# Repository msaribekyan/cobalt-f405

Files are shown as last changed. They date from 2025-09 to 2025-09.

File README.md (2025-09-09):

# Cobalt F405

## An open source flight controller based on the STM32F405 microcontroller

Custom designed flight controller for quadcopters and more.

<div style="text-align:center;">
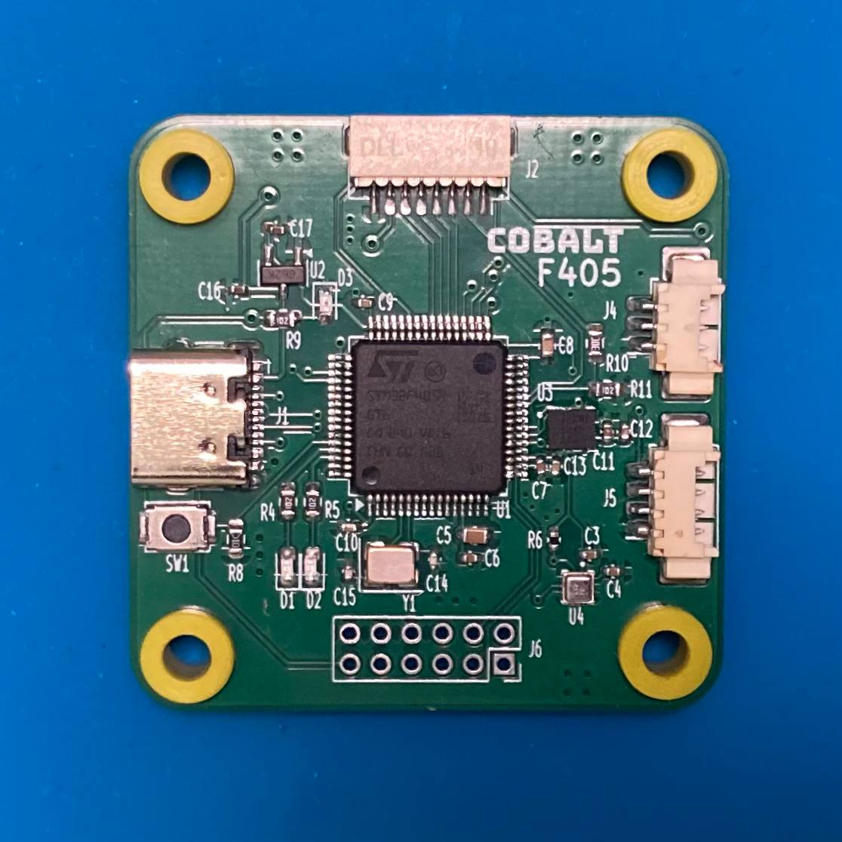
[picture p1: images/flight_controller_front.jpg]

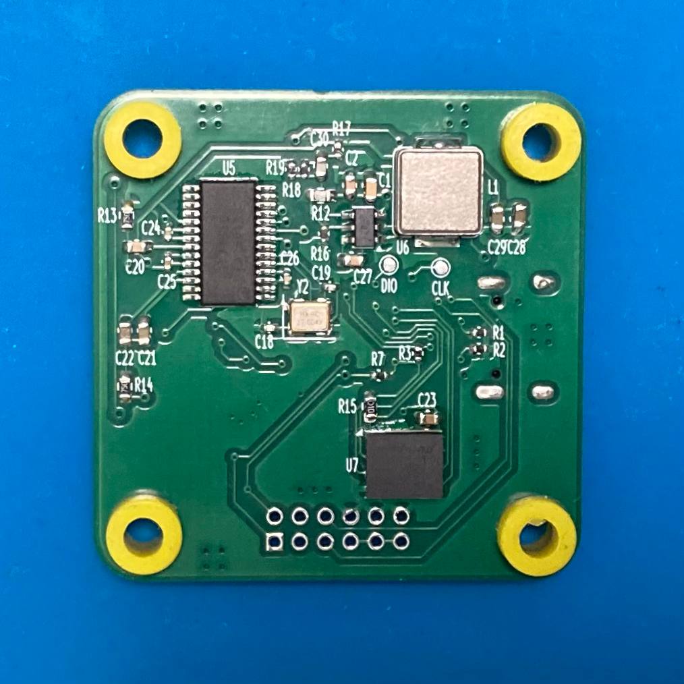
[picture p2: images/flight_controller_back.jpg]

</div>

## Features

Cobalt F405 flight controller has the following features:
- 4 motor outputs
- barometer and blackbox
- analog on-screen display
- easy-to-use connectors for camera and VTx
- USB Type-C connector for configuration
- high power 5 volt regulator

## Firmware

The flight controller was tested with the [Betaflight](https://github.com/betaflight/betaflight) firmware.

<div style="text-align:center;">
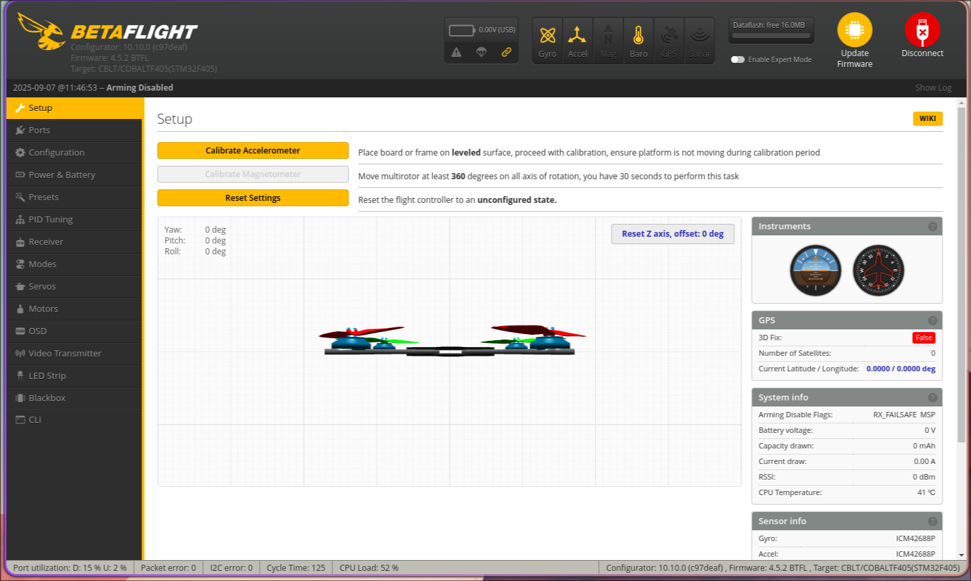
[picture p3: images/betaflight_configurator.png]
Betaflight configurator

</div>

## Designing

KiCad was used for designing the schematic and the PCB.

### Schematic

<div style="text-align:center;">
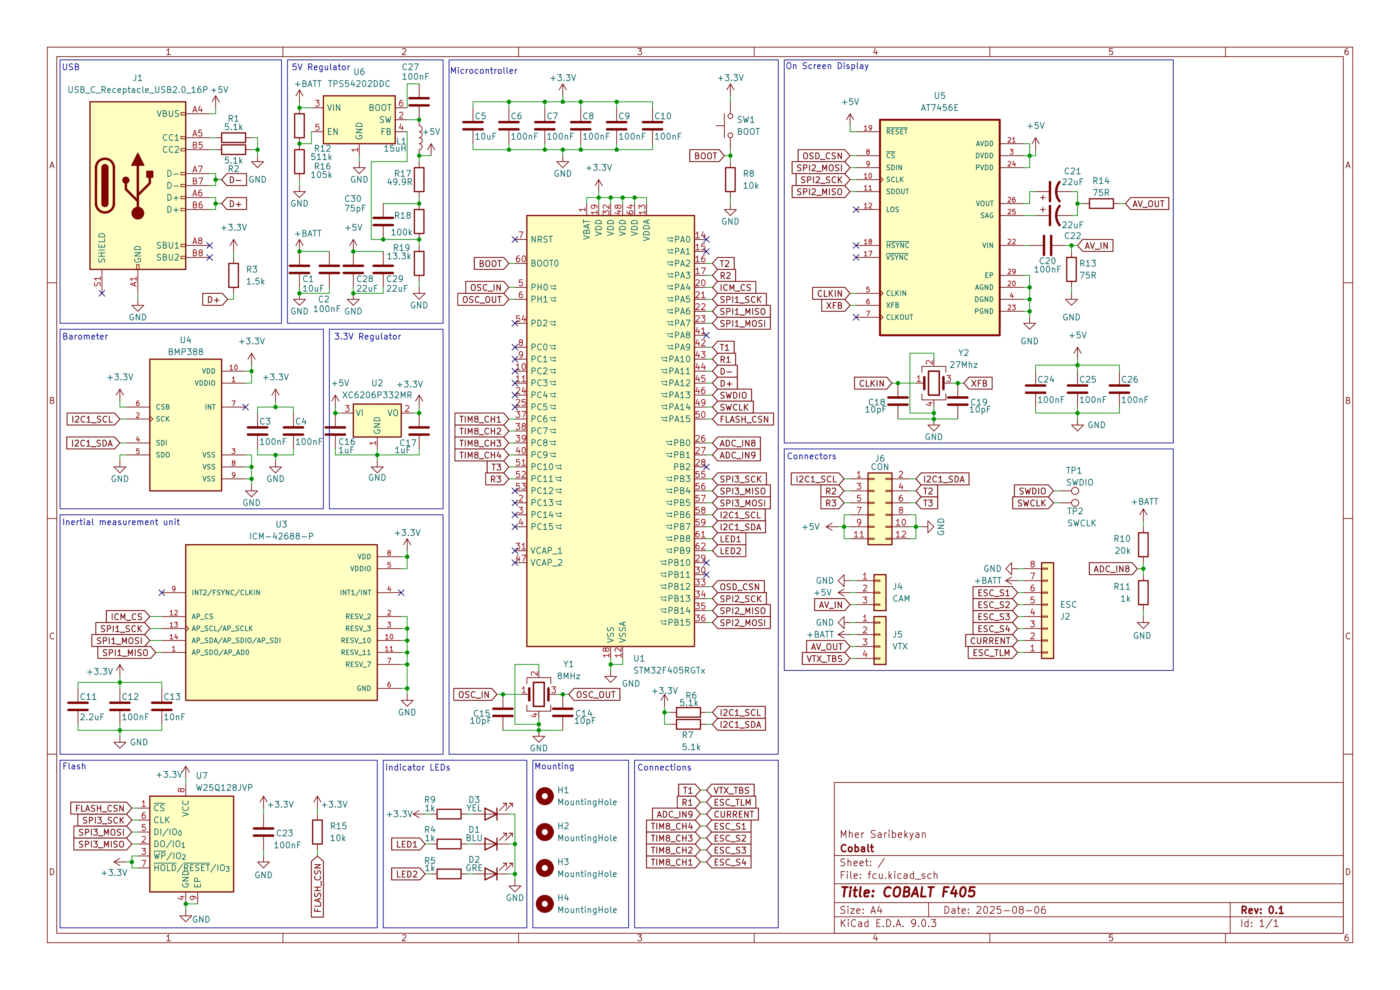
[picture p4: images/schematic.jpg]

</div>

### PCB 3D model

<div style="text-align:center;">
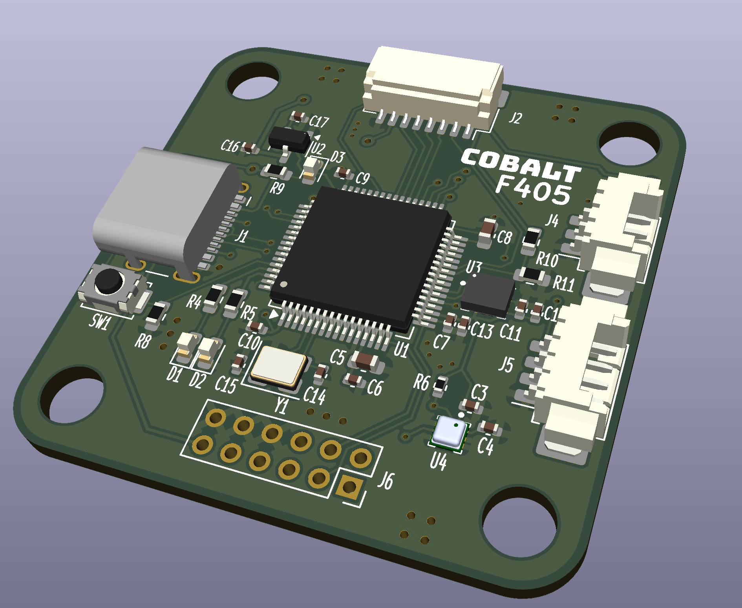
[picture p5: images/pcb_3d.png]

</div>

## Further improvements

### Microcontroller

Although the STM32F405 is still a good choice for flight controllers today, other more powerful microcontrollers also exist. [Betaflight guidlines](https://betaflight.com/docs/development/manufacturer/manufacturer-design-guidelines) suggest not using more than 4 motor outputs for STM32F4 or STM32F7 type microcontrollers.

### PCB

Two layer PCB is fine, however going to a four layer PCB with ground planes inside would reduce electrical noise, which would benefit the microcontroller and the on-board sensors.

### 9 volt regulator

Some external peripherals require higher voltage than 5 volts, however cannot accept 25 volts straight from a 6S battery. A 9 volt regulator can be added to solve this issue.

### More pads and connectors

More pads on the PCB would make it more flexible and easier to use in application. Camera and VTx connectors can be moved to more suitable locations and a connector for the radio receiver could be added.

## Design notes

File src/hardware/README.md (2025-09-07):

# The hardware

The PCB was design using [KiCad](https://gitlab.com/kicad/code/kicad), an open source schematic and PCB design software.

## Microcontroller: STM32F405RGT6

Betaflight has a list of supported microcontrollers and the STM32F405RGT6, because it is the most common and economical choice while providing enough performance.

## Inertial measurement unit: ICM-42688-P

The [Betaflight Flight Controller Manufacturer Design Guidelines](https://betaflight.com/docs/development/manufacturer/manufacturer-design-guidelines) strongly recommends against using the MPU6000 as it is end-of-life. Instead ICM-42688-P is suggested.

## Barometer: BMP388

Newer model of the BMP180 and BMP280 barometers.

## Blackbox: W25Q128JVP

Winbond W25Q128JVPIQ is a cheap and common 16 MB NOR Flash chip, with a small WSON-8 footprint.

## On-screen display: AT7456E

The flight controller has an on-screen display, for use with analog video. AT7456E is the standard choice.

## Connectors

An 8 pin JST connector is the standard for connecting to the ESC. Telemetry data is connected to UART 1 RX. The two Molex PicoBlade connectors are for the camera and the video transmitter (VTx). The camera connector passes 5 volt power, while the VTx connector passes battery power for more powerful VTx and also has a SmartAudio pin connected to UART 1 TX.

## UART, I2C and power outputs

UARTs 2 and 3 are available on the solder points, along with the I2C bus and three pairs of 5 volt and ground connections.

## PCB

## Front layers

<div style="text-align:center;">
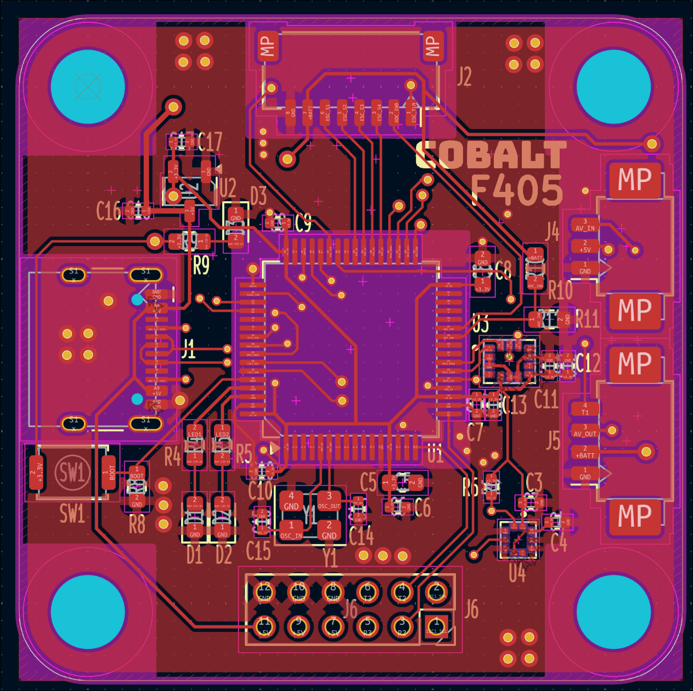
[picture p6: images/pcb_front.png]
PCB front layers

</div>

### Back layers

<div style="text-align:center;">
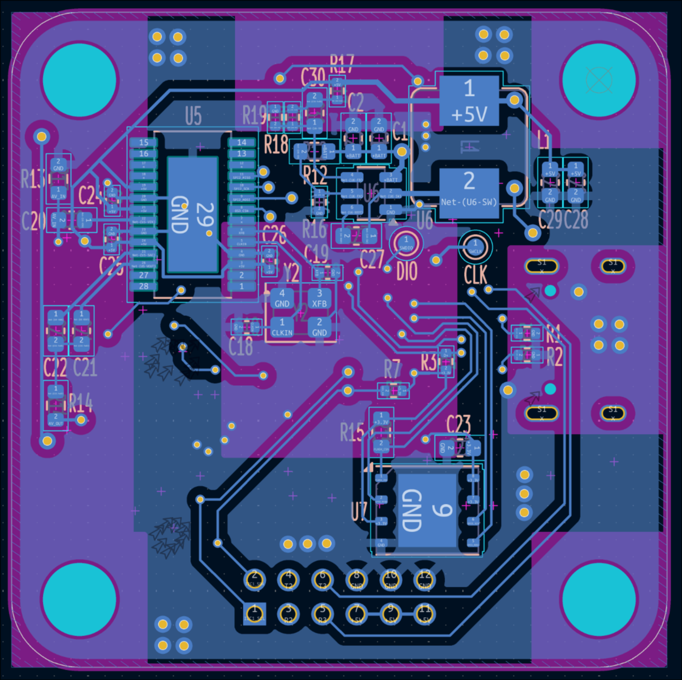
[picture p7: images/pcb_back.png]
PCB back layers

</div>

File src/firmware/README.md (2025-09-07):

# The firmware

The [Betaflight](https://github.com/betaflight/betaflight) firmware was used and tested for the flight controller. The compiled .hex file can be used to flash the firmware, however the configuration files are also avaible, in case you want to compile yourself.

## How to flash

The easiest way of flashing is using the STM32CubeProgrammer, however other methods also exist e.g. using [stlink utility](https://github.com/stlink-org/stlink) or [OpenOCD](https://github.com/openocd-org/openocd).

### Step 1
Install [STM32CubeProgrammer](https://www.st.com/en/development-tools/stm32cubeprog.html). 

### Step 2
While holding the button on the flight controller plug the USB-C cable, connect to the computer and release the button. This puts the microcontroller in DFU mode and allows flashing over USB.

### Step 3

Open STM32CubeProgrammer and from the dropdown select USB, then a device should appear in the Port section. If not, redo the Step 2, until it appears.

<div style="text-align:center;">
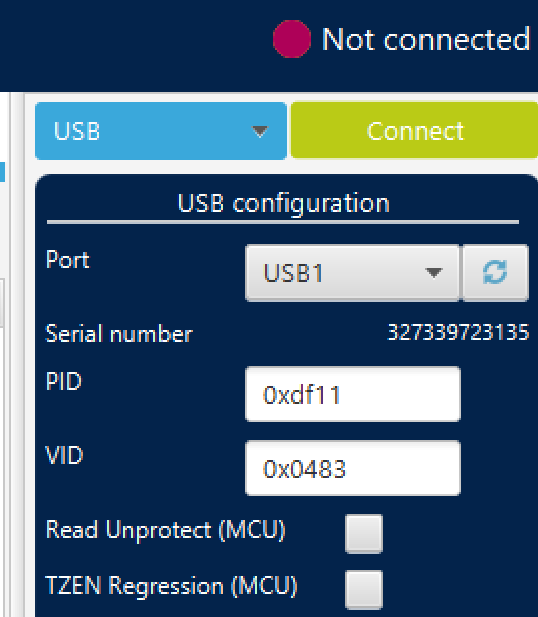
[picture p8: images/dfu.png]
Programmer DFU

</div>

Click connect.

### Step 3

Go the the Erasing & Programming tab. Click on Full chip erase.

<div style="text-align:center;">
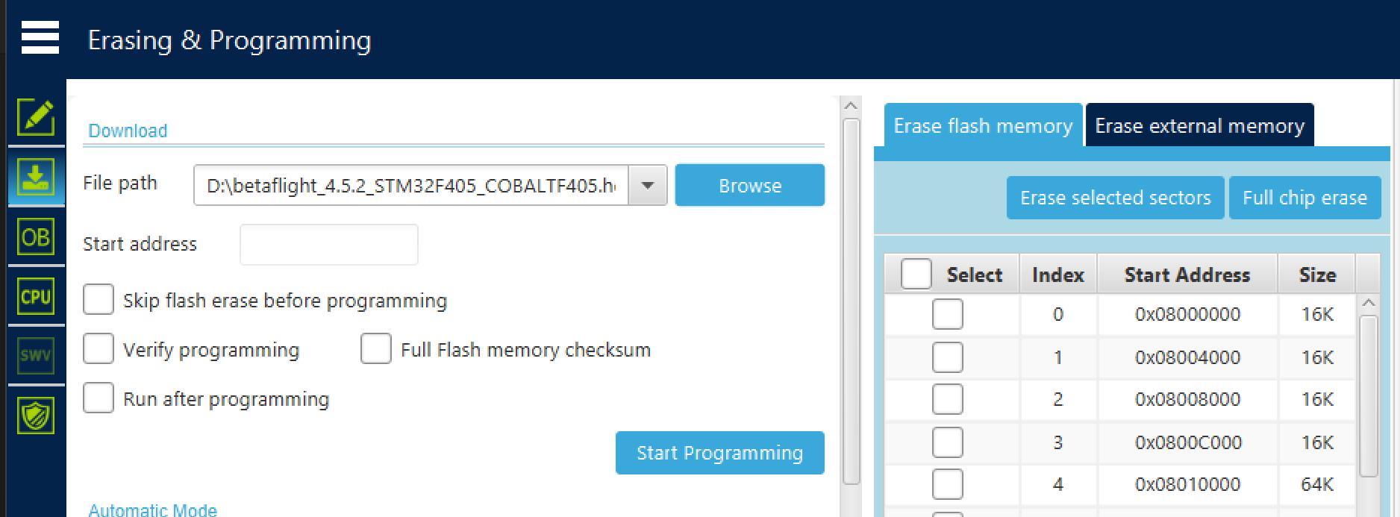
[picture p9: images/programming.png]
Programming tab

</div>

After the chip erase, select the .hex file included in the repository and click Start Programming. Wait until the firware is completely flashed, it may take a while.

### Done

Unplug and replug the USB cable. Now you should be able to connect to it using the [Betaflight App](https://github.com/betaflight/betaflight-configurator).

<div style="text-align:center;">
Betaflight configurator
</div>

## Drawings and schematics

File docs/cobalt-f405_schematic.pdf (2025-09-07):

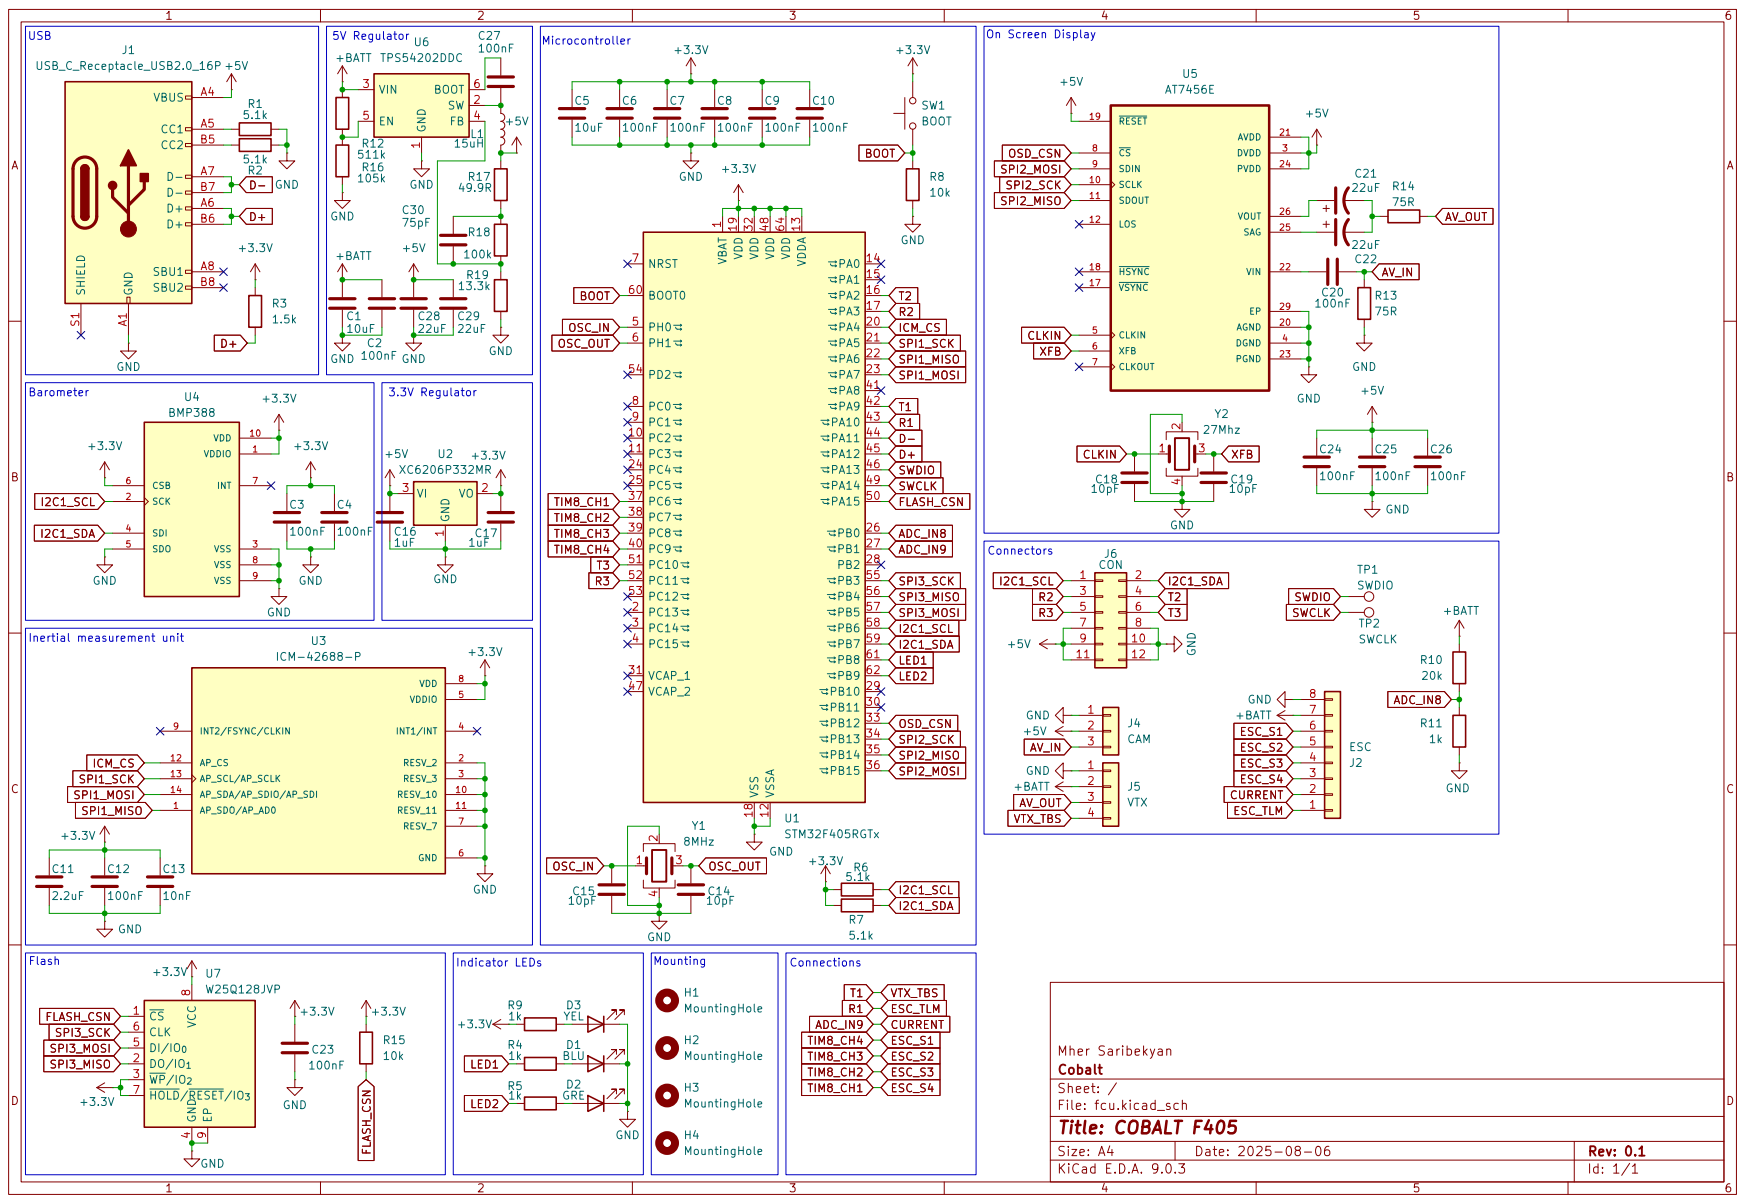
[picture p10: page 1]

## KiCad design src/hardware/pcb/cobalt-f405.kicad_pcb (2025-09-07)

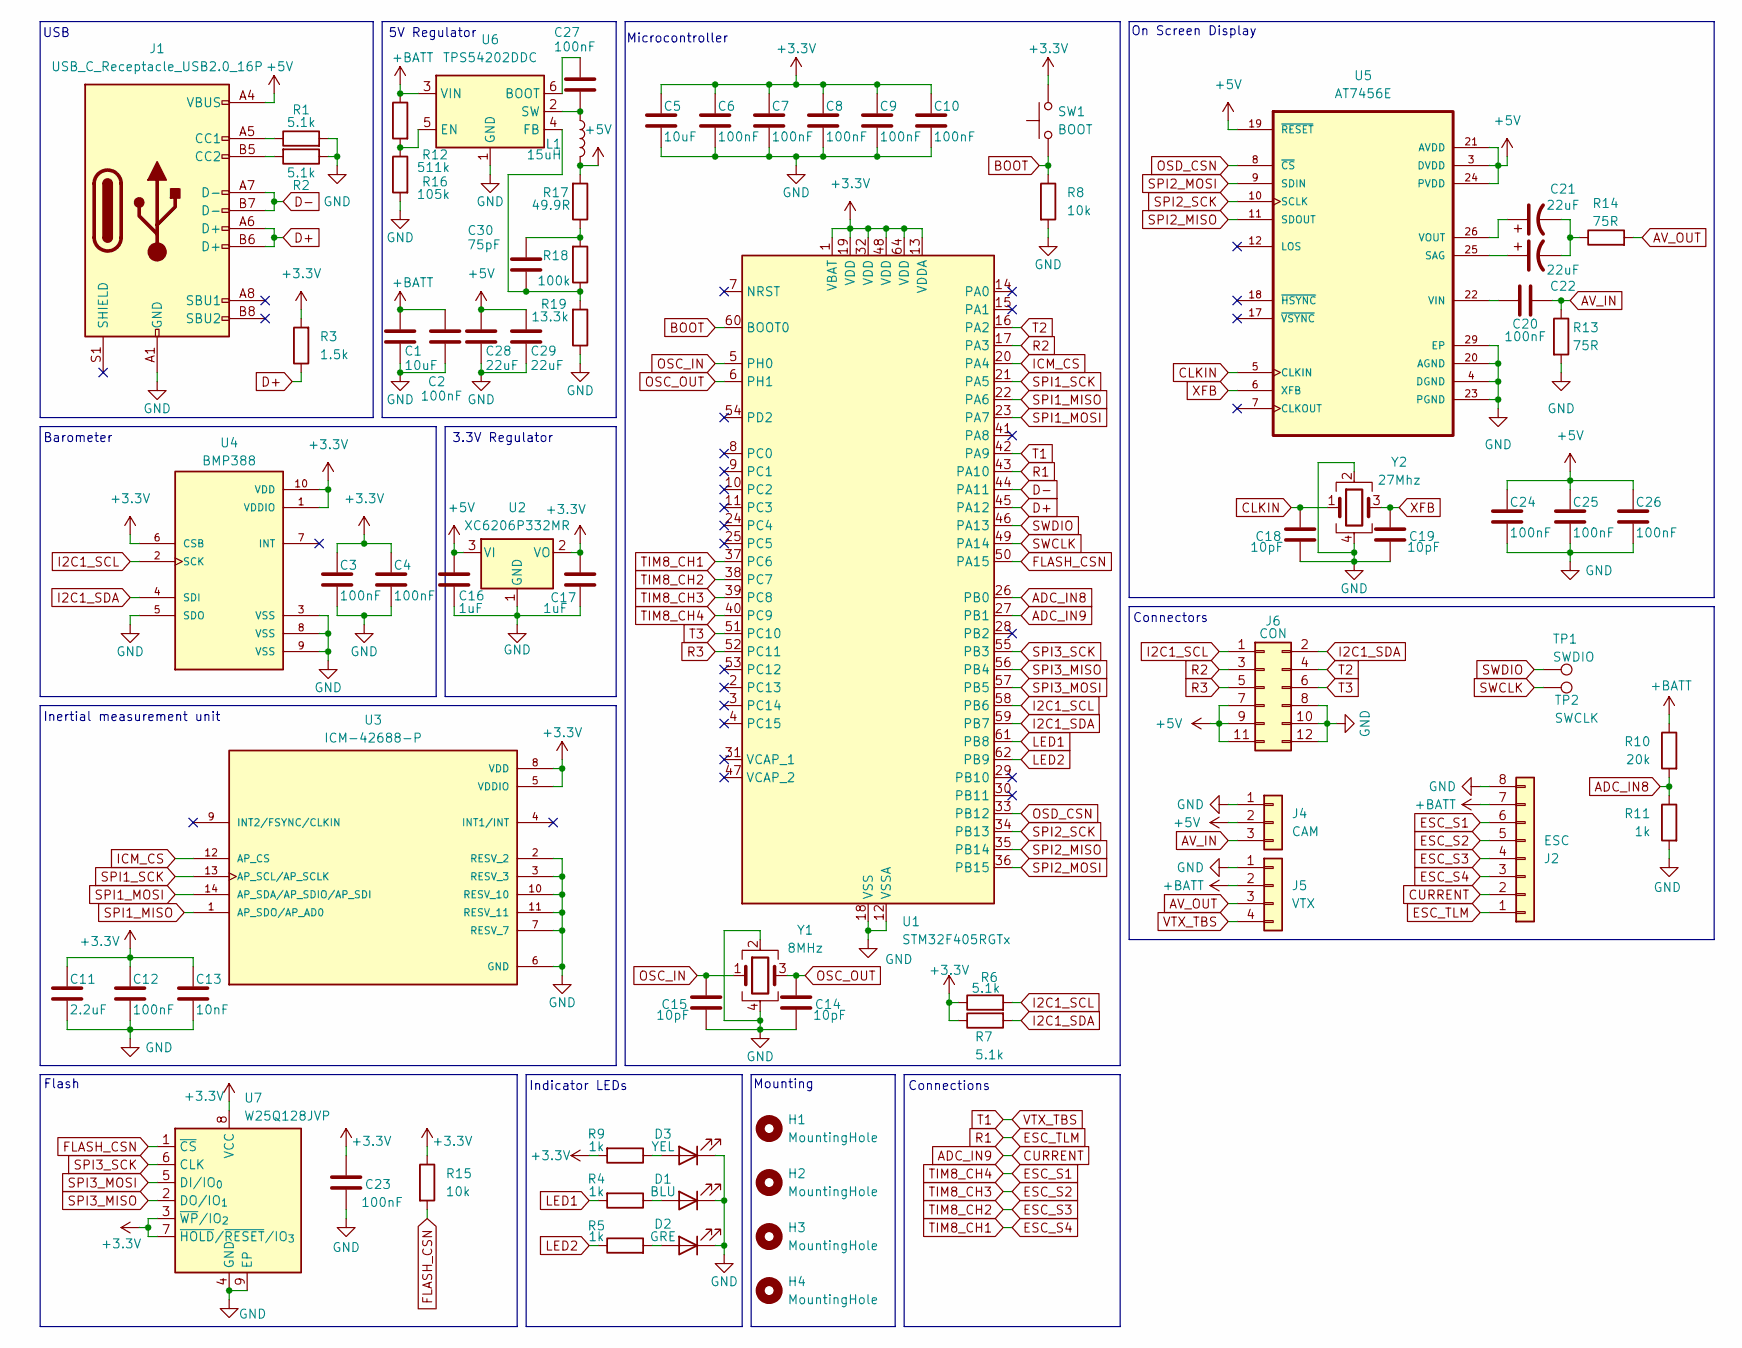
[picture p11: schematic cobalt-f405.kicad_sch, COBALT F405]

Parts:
C1, C5: 10uF; C_0603_1608Metric
C2, C8, C20, C23, C27: 100nF; C_0603_1608Metric
C3, C4, C6, C7, C9, C10, C12, C24, C25, C26: 100nF; C_0402_1005Metric
C11: 2.2uF; C_0402_1005Metric
C13: 10nF; C_0402_1005Metric
C14, C15, C18, C19: 10pF; C_0402_1005Metric
C16, C17: 1uF; C_0402_1005Metric
C21, C22, C28, C29: 22uF; C_0603_1608Metric
C30: 75pF; C_0603_1608Metric
D1: BLU; LED_0603_1608Metric
D2: GRE; LED_0603_1608Metric
D3: YEL; LED_0603_1608Metric
H1, H2, H3, H4: MountingHole; MountingHole_4.3mm_M4_ISO14580
J1: USB_C_Receptacle_USB2.0_16P; USB_C_Receptacle_HCTL_HC-TYPE-C-16P-01A
J2: ESC; JST_SH_SM08B-SRSS-TB_1x08-1MP_P1.00mm_Horizontal
J4: CAM; Molex_PicoBlade_53261-0371_1x03-1MP_P1.25mm_Horizontal
J5: VTX; Molex_PicoBlade_53261-0471_1x04-1MP_P1.25mm_Horizontal
J6: CON; PinSocket_2x06_P2.00mm_Vertical
L1: 15uH; L_Bourns_SRP7028A_7.3x6.6mm
R1, R2, R6, R7: 5.1k; R_0402_1005Metric
R3: 1.5k; R_0402_1005Metric
R4, R5, R9, R11: 1k; R_0603_1608Metric
R8, R15: 10k; R_0603_1608Metric
R10: 20k; R_0603_1608Metric
R12: 511k; R_0603_1608Metric
R13, R14: 75R; R_0603_1608Metric
R16: 105k; R_0402_1005Metric
R17: 49.9R; R_0402_1005Metric
R18: 100k; R_0402_1005Metric
R19: 13.3k; R_0402_1005Metric
SW1: BOOT; SW_Push_SPST_NO_Alps_SKRK
TP1: SWDIO; TestPoint_Pad_D1.0mm
TP2: SWCLK; TestPoint_Pad_D1.0mm
U1: STM32F405RGTx; LQFP-64_10x10mm_P0.5mm
U2: XC6206P332MR; SOT-23-3
U3: ICM-42688-P; PQFN50P300X250X97-14N; PARTREV 1.2
U4: BMP388; PQFN50P200X200X80-10N; PARTREV 1.1
U5: AT7456E; SOP65P637X110-28N
U6: TPS54202DDC; SOT-23-6
U7: W25Q128JVP; WSON-8-1EP_6x5mm_P1.27mm_EP3.4x4.3mm
Y1: 8MHz; Crystal_SMD_3225-4Pin_3.2x2.5mm
Y2: 27Mhz; Crystal_SMD_3225-4Pin_3.2x2.5mm

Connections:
+3.3V: C3.1, C4.1, C5.1, C6.1, C7.1, C8.1, C9.1, C10.1, C11.1, C12.1, C13.1, C17.1, C23.1, R3.2, R6.1, R7.1, R9.2, R15.1, SW1.2, U1.1 (VBAT), U1.13 (VDDA), U1.19 (VDD), U1.32 (VDD), U1.48 (VDD), U1.64 (VDD), U2.2 (VO), U3.5 (VDDIO), U3.8 (VDD), U4.1 (VDDIO), U4.6 (CSB), U4.10 (VDD), U7.3 (~WP/IO_{2}), U7.7 (~HOLD/~RESET/IO_{3}), U7.8 (VCC)
+5V: C16.1, C24.1, C25.1, C26.1, C28.1, C29.1, J1.A4 (VBUS), J1.A9 (VBUS), J1.B4 (VBUS), J1.B9 (VBUS), J4.2, J6.7, J6.9, J6.11, L1.1, R17.2, U2.3 (VI), U5.3 (DVDD), U5.19 (~RESET), U5.21 (AVDD), U5.24 (PVDD)
+BATT: C1.1, C2.1, J2.7, J5.2, R10.1, R12.1, U6.3 (VIN)
ADC_IN8: R10.2, R11.1, U1.26 (PB0)
ADC_IN9: J2.2, U1.27 (PB1)
AV_IN: C20.2, J4.3, R13.1
AV_OUT: J5.3, R14.2
BOOT: R8.1, SW1.1, U1.60 (BOOT0)
CLKIN: C18.1, U5.5 (CLKIN), Y2.1
D+: J1.A6 (D+), J1.B6 (D+), R3.1, U1.45 (PA12)
D-: J1.A7 (D-), J1.B7 (D-), U1.44 (PA11)
ESC_S1: J2.6, U1.40 (PC9)
ESC_S2: J2.5, U1.39 (PC8)
ESC_S3: J2.4, U1.38 (PC7)
ESC_S4: J2.3, U1.37 (PC6)
ESC_TLM: J2.1, U1.43 (PA10)
FLASH_CSN: R15.2, U1.50 (PA15), U7.1 (~CS)
GND: C1.2, C2.2, C3.2, C4.2, C5.2, C6.2, C7.2, C8.2, C9.2, C10.2, C11.2, C12.2, C13.2, C14.2, C15.2, C16.2, C17.2, C18.2, C19.2, C23.2, C24.2, C25.2, C26.2, C28.2, C29.2, D1.1 (K), D2.1 (K), D3.1 (K), J1.A1 (GND), J1.A12 (GND), J1.B1 (GND), J1.B12 (GND), J2.8, J4.1, J5.1, J6.8, J6.10, J6.12, R1.2, R2.1, R8.2, R11.2, R13.2, R16.2, R19.1, U1.12 (VSSA), U1.18 (VSS), U1.63 (VSS), U2.1 (GND), U3.2 (RESV_2), U3.3 (RESV_3), U3.6 (GND), U3.7 (RESV_7), U3.10 (RESV_10), U3.11 (RESV_11), U4.3 (VSS), U4.5 (SDO), U4.8 (VSS), U4.9 (VSS), U5.4 (DGND), U5.20 (AGND), U5.23 (PGND), U5.29 (EP), U6.1 (GND), U7.4 (GND), U7.9 (EP), Y1.2, Y1.4, Y2.2, Y2.4
I2C1_SCL: J6.1, R6.2, U1.58 (PB6), U4.2 (SCK)
I2C1_SDA: J6.2, R7.2, U1.59 (PB7), U4.4 (SDI)
ICM_CS: U1.20 (PA4), U3.12 (AP_CS)
LED1: R4.2, U1.61 (PB8)
LED2: R5.1, U1.62 (PB9)
unnamed: C21.2, C22.2, R14.1
unnamed: C30.2, R17.1, R18.2
unnamed: D1.2 (A), R4.1
unnamed: D2.2 (A), R5.2
unnamed: D3.2 (A), R9.1
unnamed: J1.A5 (CC1), R1.1
unnamed: J1.B5 (CC2), R2.2
unnamed: C22.1, U5.25 (SAG)
unnamed: C20.1, U5.22 (VIN)
unnamed: C21.1, U5.26 (VOUT)
unnamed: C27.2, U6.6 (BOOT)
unnamed: R12.2, R16.1, U6.5 (EN)
unnamed: C30.1, R18.1, R19.2, U6.4 (FB)
unnamed: C27.1, L1.2, U6.2 (SW)
OSC_IN: C15.1, U1.5 (PH0), Y1.1
OSC_OUT: C14.1, U1.6 (PH1), Y1.3
OSD_CSN: U1.33 (PB12), U5.8 (~CS)
R2: J6.3, U1.17 (PA3)
R3: J6.5, U1.52 (PC11)
SPI1_MISO: U1.22 (PA6), U3.1 (AP_SDO/AP_AD0)
SPI1_MOSI: U1.23 (PA7), U3.14 (AP_SDA/AP_SDIO/AP_SDI)
SPI1_SCK: U1.21 (PA5), U3.13 (AP_SCL/AP_SCLK)
SPI2_MISO: U1.35 (PB14), U5.11 (SDOUT)
SPI2_MOSI: U1.36 (PB15), U5.9 (SDIN)
SPI2_SCK: U1.34 (PB13), U5.10 (SCLK)
SPI3_MISO: U1.56 (PB4), U7.2 (DO/IO_{1})
SPI3_MOSI: U1.57 (PB5), U7.5 (DI/IO_{0})
SPI3_SCK: U1.55 (PB3), U7.6 (CLK)
SWCLK: TP2.1, U1.49 (PA14); also elsewhere on the board
SWDIO: TP1.1, U1.46 (PA13); also elsewhere on the board
T1: J5.4, U1.42 (PA9)
T2: J6.4, U1.16 (PA2)
T3: J6.6, U1.51 (PC10)
XFB: C19.1, U5.6 (XFB), Y2.3

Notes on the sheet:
Connectors
Microcontroller
5V Regulator
3.3V Regulator
Connections
Inertial measurement unit
Indicator LEDs
USB
On Screen Display
Barometer
Flash
Mounting

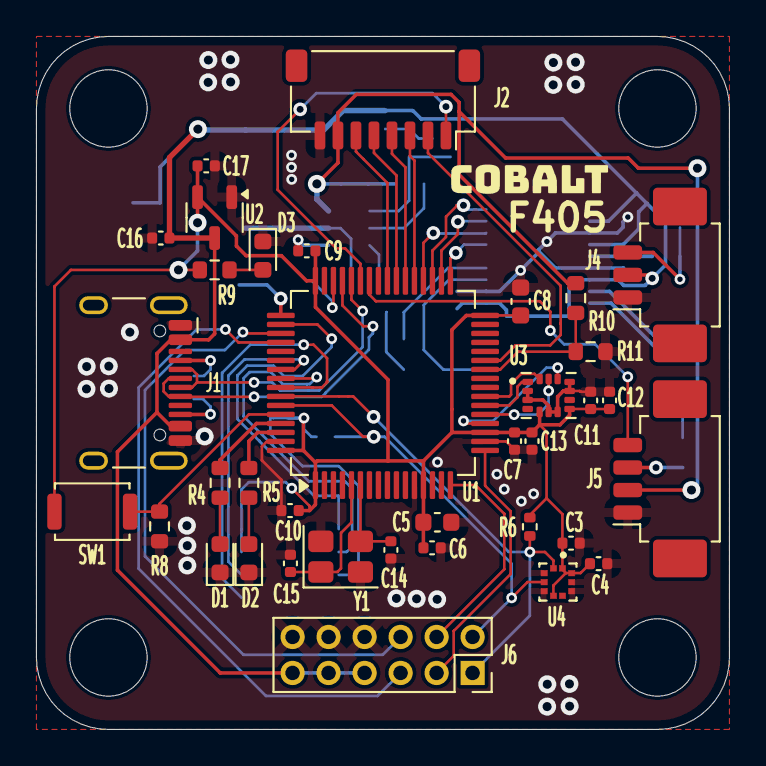
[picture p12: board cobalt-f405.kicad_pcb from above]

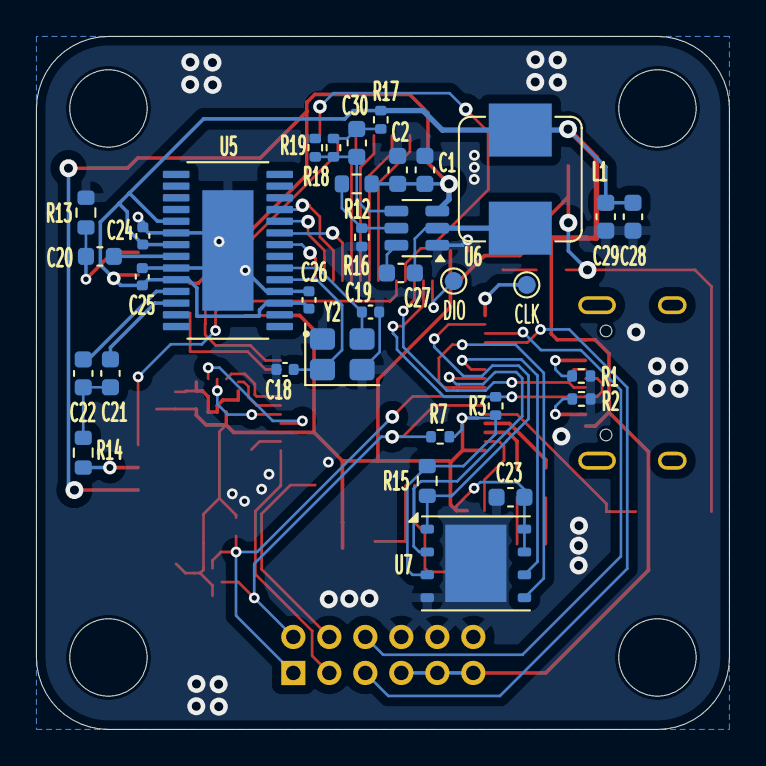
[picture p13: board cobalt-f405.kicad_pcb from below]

Board: 2 copper layers, 38.5 x 38.5 mm, 74 parts (34 on the bottom side), 57 nets.

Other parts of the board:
CLK: SWCLK; TestPoint_Pad_D1.0mm
DIO: SWDIO; TestPoint_Pad_D1.0mm

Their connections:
SWCLK: CLK.1; also elsewhere on the board
SWDIO: DIO.1; also elsewhere on the board

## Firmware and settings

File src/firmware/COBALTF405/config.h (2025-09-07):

#pragma once

#define FC_TARGET_MCU			STM32F405

#define BOARD_NAME			COBALTF405
#define MANUFACTURER_ID			CBLT

#define USE_GYRO
#define USE_GYRO_SPI_ICM42688P
#define USE_ACC
#define USE_ACC_SPI_ICM42688P
#define USE_BARO_BMP388
#define USE_MAX7456
#define USE_FLASH
#define USE_FLASH_W25Q128FV

#define MOTOR1_PIN			PC9
#define MOTOR2_PIN			PC8
#define MOTOR3_PIN			PC7
#define MOTOR4_PIN			PC6

#define UART1_TX_PIN			PA9
#define UART2_TX_PIN			PA2
#define UART3_TX_PIN			PC10
#define UART1_RX_PIN			PA10
#define UART2_RX_PIN			PA3
#define UART3_RX_PIN			PC11

#define I2C1_SCL_PIN			PB6
#define I2C1_SDA_PIN			PB7

#define LED0_PIN			PB8
#define LED1_PIN			PB9

#define SPI1_SCK_PIN			PA5
#define SPI2_SCK_PIN			PB13
#define SPI3_SCK_PIN			PB3

#define SPI1_SDI_PIN			PA6
#define SPI2_SDI_PIN			PB14
#define SPI3_SDI_PIN			PB4

#define SPI1_SDO_PIN			PA7
#define SPI2_SDO_PIN			PB15
#define SPI3_SDO_PIN			PB5

#define ADC_VBAT_PIN			PB0
//#define ADC_CURR_PIN			PB1

#define FLASH_CS_PIN			PA15
#define MAX7456_SPI_CS_PIN		PB12
#define GYRO_1_CS_PIN			PA4

#define TIMER_PIN_MAPPING \
    TIMER_PIN_MAP( 0, MOTOR1_PIN, 2,  0) \
    TIMER_PIN_MAP( 1, MOTOR2_PIN, 2,  1) \
    TIMER_PIN_MAP( 2, MOTOR3_PIN, 2,  1) \
    TIMER_PIN_MAP( 3, MOTOR4_PIN, 2,  0)

#define ADC1_DMA_OPT			0
#define USE_BARO
#define BARO_I2C_INSTANCE		I2CDEV_1
//#define DEFAULT_CURRENT_METER_SOURCE    CURRENT_METER_ADC
#define DEFAULT_VOLTAGE_METER_SOURCE    VOLTAGE_METER_ADC
#define DEFAULT_VOLTAGE_METER_SCALE     210
//#define DEFAULT_CURRENT_METER_SCALE	250
//#define DEFAULT_CURRENT_METER_OFFSET	-500
#define SYSTEM_HSE_MHZ			8
#define DEFAULT_BLACKBOX_DEVICE		BLACKBOX_DEVICE_FLASH
#define MAX7456_SPI_INSTANCE		SPI2
#define FLASH_SPI_INSTANCE		SPI3
#define GYRO_1_SPI_INSTANCE		SPI1
#define GYRO_1_ALIGN			CW90_DEG
#define SERIALRX_UART			SERIAL_PORT_USART2
#define DEFAULT_RX_FEATURE		FEATURE_RX_SERIAL
